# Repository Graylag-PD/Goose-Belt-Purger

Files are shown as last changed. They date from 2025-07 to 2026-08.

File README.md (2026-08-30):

**BRANTA Branch** - This is a second major iteration of the GBP. Everything is work-in progress and anything can change withou warning, but if you want to testsome newest ideas, you are welcome. For more stable product look into an ANSER Branch
________________________________________

# Goose Belt Purger (GBP)
A simple, lightweight, and low-cost belt purger for 3D printers.\
An alternative to blob-producing purging routines and devices, or traditional purging into towers.\
Officially supported printers are Voron Trident and 2.4, but it is small and light enough to be adapted for other printers.

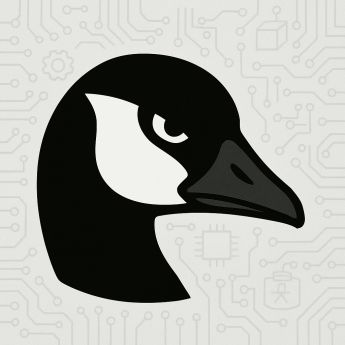
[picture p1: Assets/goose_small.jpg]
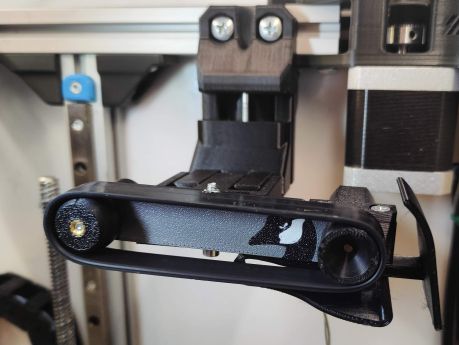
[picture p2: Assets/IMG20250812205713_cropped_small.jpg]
   
  
See also our [promo video](https://youtu.be/ZBZhAEFlKdA) on YouTube, or slightly older [video](https://youtu.be/MWTFuGqhi_c) with more detailed depiction of purger in action.
  
Currently in Beta testing — proven as a functional design, but can have unexpected issues and design might change any time.  
  
If you have any questions, you can visit my [Discord server](https://discord.gg/8a29q9gJb9).  
  
If you find this useful, a like or a make on [Printables](https://www.printables.com/model/1371713-goose-belt-purger-gbp) helps others discover and trust the design.

# About
Like many makers, I've been fascinated by single-nozzle multicolor/multimaterial printing. But like many, I hate purge towers. They can be large, ugly, and take up valuable print bed space. This is why I was intrigued by the Blobifier — but there are several issues. First, I use a Voron Trident, which isn't compatible. While there are adaptations of the Blobifier concept for the Trident, none have gained significant traction. Second, both the original Blobifier and its Trident adaptations generally share the drawback that each purge requires toolhead parking near the bed edge, blocking part of the bed and potentially risking collisions. Third, the produced blobs are volumetrically inefficient. Even though the blobs are relatively compact, their shape means they can't utilize the waste bin space effectively. This is even worse with the loose coil "poops" produced by some printers.

There had to be a better way.

And then it struck me — use a belt to produce compact "line" purges. To be fair, this isn't an entirely new idea. There have been mods involving purging on stationary aluminum platforms or kinematic belts, but none of those options felt right. I wanted something simple, affordable, and buildable from stuff you already have lying around your workshop.\
This is why the Goose Belt Purger was created.

What does it have to do with geese? Nothing. I just like geese.

# Design

The core of the GBP is a silicone wristband — the kind you can get anywhere, often for free. The most common size, which GBP is designed around, is 12 mm wide and 20 cm in circumference. You can use any similar band, even ones with embossing or printing, since we'll use the smooth inner surface. Changing the belt is easy, so use whatever you have and swap it later if needed.

Silicone rubber is ideal for this use. When filament is extruded onto the smooth side, it sticks but releases easily at the end of the straight belt section. Silicone is heat-resistant enough to endure the nozzle heat, provided it keeps moving. However, if the nozzle stays in one place too long, the band will discolor (brown or black) or even burn.

The belt moves along two printed pulleys. How does it stay in place without flanges? Dark magic. Don't ask.

One pulley is driven by a cheap miniature DC motor with a gearbox.  A 50rpm or slower version is recommended, up to 15rpm if you want really thick extrusions. &#x20;

> [!WARNING]\
> Motor is an inductive component. Skipping the recommended protection (e.g. flyback diode) can cause voltage spikes and permanent damage to your controller.  
>  
>Read the “Electrical connection” section and install all safety components.  
>Use at your own risk.  

The other pulley spins freely on a tilting arm. The arm pivots on a bearing around the motor shaft and is pushed upward by a pair of magnets acting as springs. The arm's purpose is to press against the nozzle but move away to avoid collisions with the nozzle or printhead.

GBP is mounted using an Armored Turtle brush mount or universal Klicky style mount. But you can also design your own mount and connect it with AT mount styled dovetails.

# Bill of Materials (BOM)
## Purger
- 1x Silicone wristband (12 mm wide, 200 mm circumference)
- 1x DC motor, 12 mm diameter, 6V/12V, 15rpm — commonly sold as GA12 N20 or N30. See note below.
- 3x 623 bearings
- 2x 6x3 mm magnets (Voron standard size)
- 3x heat-set insert M3x5x4 (Voron standard size)
  
If your board supports 5V on fan outputs, you may use a 6V motor. If only 24V is available, use a 12V motor with <50% PWM.  
Initial testing shows optimal belt speed under load is 2–12rpm, so the 15rpm seems to be ok. PWM can reduce speed to \~5–10% of rated speed. 30rpm and 50rpm motors also seem to be usable  

**M3 hardware:**

- 1x M3 nut
- 1x M3 nylock nut*
- 1x M3x6 set screw
- 1x M3x20 SHCS*
- 2x M3x20 FHCS
- 1x M3x30 SHCS
  
*) If you have trouble getting a M3 nyloc, you can instead use HSI variant of arm - replace nylock nut for one more heat-set insert, M3x16 SHCS instead of M3x20 SHCS and get some threadlocker  

**Electrical components:**
- Schottky diode 1A (e.g. 1N5819) - For 5V or 12V supply voltage  
or
- Schottky diode 2A (e.g. 1N5820) - For 24V supply voltage together with 12V motor  
- Resistor 47R
- Ceramic capacitor 10 nF, 50V 
  
If you don't like the idea of soldering those parts, you can also get yourself a **[MicroFlip](https://github.com/Trondle-Embeeded-Systems/MicroFlip)** board, which already has everything.

## Mounts
**AT mount**  
Applies to Voron Trident or similar printer together with modified (shorter) AT mount files  
- 2x heat-set insert M3x5x4 (Voron standard size)
- 2x M3 nyloc nut
- 2x M3x8 SHCS
- 1x M3x35 SHCS (you can use M3x30 if you have trouble getting it)
- 1x M3x25 SHCS

**Klicky style mount**  
Universal solution  
- 8x heat-set insert M3x5x4 (Voron standard size)
- 8x M3x8 SHCS

# Build Instructions

Build instructions can be found [here](assembly.md).

# Electrical Connection

Connect the DC motor to any free power output on your controller board, preferably a fan output. If possible, supply it with 5V or 12V to minimize heating. Otherwise, reduce voltage via PWM.

> [!IMPORTANT]\
> The DC motor is a strong inductive load and will generate large voltage spikes, which can destroy your board's MOSFET or even the MCU if untreated. At minimum, use a properly sized Schottky flyback diode across the board output. I also recommend an RC snubber on the motor terminals.
>
> Some boards (e.g., BTT Octopus) already include protection diodes. Others rely only on the MOSFET's internal diode, which is usually insufficient. You can check comprehensive table [here](board_list.md), or consult your board's schematic.  When unsure, ask someone.
>
> For the RC snubber, I used a 47 Ω resistor and a 10 nF, 50V ceramic capacitor. Solder one leg of each component together, then solder the free legs to the motor terminals. This configuration dampens voltage spikes while preserving PWM response. You may use a larger capacitor for extra safety, but note that increased capacitance degrades PWM response. Avoid using a capacitor alone (without resistor), as this can cause resonance and make things worse.

I confirmed the effectiveness of these measures with an oscilloscope, but I can't guarantee that no fast transients were missed (e.g., during PWM changes). Data is still limited, so proceed with care and understand what you're doing.

If you want some better alternative to manually soldering components to motor, see amazing [MicroFlip](https://github.com/Trondle-Embeeded-Systems/MicroFlip) project by Ntrondle. You can make it yourself, or check our Discord if anyone has any boards for sale. Keep in mind, that MicroFlip is **not** developed as part of this project. If you like it and would like to support its creator, do so on his GitHub page.  

# Software and Slicer Configuration
For more information about provided configuration file, slicer configuration and integration into AFC or Happy Hare, please look [here](sw_configuration.md).

# Tips and Observations
 
Extrude onto the smooth inner side of the wristband. You can try the outer side, but adhesion is generally worse and requires an unembossed, unprinted band — which is surprisingly hard to find. The inner surface sticks well, even without direct nozzle contact, while the outer side requires pressure that magnets alone can't provide.

Adhesion heavily depends on belt speed. If filament doesn't stick, slow the belt. Once adhesion starts, the extruded line tends to pull more material from the nozzle. 
  
Adhesion is also strongly dependant on filament drynes. Wet filament tends to curl up and does not stick to belt as easilly.

The macro splits the purge into short "toothpicks" or pellets to improve waste volume efficiency.

Initial testing shows optimal belt speed is 2–12rpm (roughly 1.8–11 mm/s or 108–660 mm/min). The easiest way to measure speed is to mark a spot on a pulley, start a stopwatch, and time 10 full revolutions.

Don't be afraid to experiment with the macro parameters. Every printer is unique, so expect to tune it up for a some time untill you hit the 'just right' zone.

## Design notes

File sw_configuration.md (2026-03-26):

# Configuration file and macro configuration
Default control software is the [Goose Purge Macro](https://github.com/Graylag-PD/Goose-Purge-Macro). For details on installation, see there.  
Information in this file apply to macro version v0.8.2 or newer. If you have any kind of issues, check first, if you are on newest available version.  
  
The old version of the macro (v0.7.3) remains within the Goose Belt Purger repository and is now considered a legacy solution. 

## Macro configuration
Macro can be configured by changing the variables in `goose_purge.cfg` file. See comments in the file and adapt it to your printer.  

Once set up, the purge routine can be triggered by running the G-code macro:  
 - `GOOSE_PURGE PURGE_VOLUME=###`  
   or  
 - `GOOSE_PURGE PURGE_LENGTH=###`  
where ### is the purge volume in mm³ or length in mm. If both are provided, they are added up. If neither is provided, the macro runs according default value variable configured within the macro.

Below are the most common "chokepoints" for the new users:  
### Output pin definition
This part is usually straight forward and the only difficulty may come from identifying correct MCU pin(s). For this you need to consult your board documenatation.  
  
For a DC motor, use a fan output. There is hovewer a catch - although any fan output can be used, or in fact any output pin, not all pins are capable of a HW PWM and this may apply even to pins which should be HW PWM capable from chip design. 
This is not a bug, but comes from the way Klipper is configured. If you run into situation, that everything is connected and configured correctly but the motor still does not activates, consider changing the output which you are using.  
If for whatever reason you cannot use any other port, you may fall back to using the SW generated PWM, but be aware of the performance penalty this can mean.   
One example of the pin which should work but does not is the PA8 on a STM32F446.
  
### Z axis strategy
Applicable Z axis strategy depends on the purger mounting and printer type. For a Voron Trident (or similar) printers you should use "0" - no Z movement. For a Voron 2.4 and purger on the gantry you can use either strategy "0" or strategy "2". Later can help with pellets pilling up under the purger.  
For a Voron 2.4 with the purger fixed on a frame, use strategy "1" - absolute Z position.
  
### Staging and purging positions
At first you should think about your purging position. In general you have two options - either purge directly on top of your idler pulley, or to purge on a free belt span (in between pulleys). If you are in doubt, start with purging position above the idler belt, as the pressure from the idler creates more stable conditions and it maximises the cooling time for the deposited material.  
Purging on a free belt span is often used by more experienced users who aim to maximise purge thickness (to create short, thick pellets), as the belt flexes and adapts better to thick extrusions.  
  
Once you decide on your purging position, you can define your staging position. In general your staging can be anywhere, as its only purpose is to have defined safe position from which we can reach the purging position. But in practice you need to consider oozing and as such you should have your staging position as close to purging position as possible AND have it so, that by moving to purging position you wipe away any ooze. This usually means perpendiculary to the belt or between motor pulley and purging position. If you do this wrong, the ooze might be squished to the side of the nozzle where it sticks and later on causes issues.    

### Motor PWM (belt_pwm variable)
Although this parameter should be easy to configure, unfortunately there is a great variability between motors which you can buy. Some n20 motors are built for a high torque and spin well even with very low PWM duty cycles, while some motors are built for a lower torque and need considerable higher PWM. This can be most easily identified by the static coil resistance, but unfortunately this parameter is usually listed in the item description.  
Fortunately there is a simple way to determine the necessary values. Connect your (fully assembled) purger to the printer, configure the macro with a default values and restart the klipper. As soon the printer comes back online, you should see the purger in your interface (Mainsail or FLuidd) along the fans with option to control its speed with a slider. This way you can quickly try out various PWM settings without actually running the macro.  
When testing the motor, you are looking at three different thresholds. First one is the minimum start-up speed - this is the PWM value at which the motor reliably starts even from standstill. This is your safe value which you should ideally put to your macro. Next up is the minimum stable speed - this is the PWM value, at which the motor can still run reliably if kickstarted. This is usually 10% below minimum start-up speed and you can use it with correctly set kickstart paramerer. Keep in mind, that the purging itself is loading the motor and can stall it if you go too low.  
Third value is the absolute lowest speed - this is the speed, at which the motor is still able to run, but tends to stall at any kind of load. This is usually 5% below minimum stable speed. There is no practical use for this setup.  
  
Once you find the value you are happy with, set it to the macro variables, restart the klipper and do the test run of the macro just to see, that everything works as expected. 

## Useful tips
Tuning the variables "just right" can take many iterations and hitting that Save&Restart button every time can be very time consuming. Instead, you can edit your variables on the fly through terminal command `SET_GCODE_VARIABLE`, e.g. `SET_GCODE_VARIABLE MACRO=_GOOSE_PURGE_VARIABLES VARIABLE=belt_pwm VALUE=0.33` to change the belt speed. You can even do that during print job - set up a test print that has a bunch of filament changes, then adjusted the variables live as you go. Because the way klipper queues up gocode, it may not take effect immediately so if you enter this while you're in the middle of a toolchange, you won't see the results until the next toolchange.  
Keep in mind this doesn't save the values to config file, so you will have to remember to set the values in the cfg file yourself. 

## GBP and other printer firmwares
No other printer firmwares are supported as of this moment. We are open to add support for other firmwares if you are interested, however be prepared to provide extensive support for a development for your choosen platform.

# Integration of Goose Belt Purger into your print jobs

## Standalone operation (Slicer controlled)
You can use GBP in standalone mode independently on any other klipper add-ons. You can even use it this way if you don't have any MMU/AMS on your printer, e.g. for manual filament changes. Purging can be triggered manualy, or more commonly by slicer.  

Slicer configuration is following:  
For initial priming, place the `GOOSE_PURGE` command with appropriate parameter at the beginning of your **Start G-code** where you'd normally place a prime line.  
For tool changes, insert the command into **Tool change G-code** just after the `T#` command.  
Note that not all slicers support passing purge parameters. In OrcaSlicer, you can use `GOOSE_PURGE PURGE_LENGTH=[flush_length]`. In PrusaSlicer, the volume must be hardcoded.  For other slicers, consult their documentation. 

If you are using GBP in standalone mode but let filament changes handling to Happy Hare or a similar tool, configure it so it doesn't return toolhead to the previous or next G-code position to avoid unnecessary travel.  

## AFC integration 
*Contributed in full by adamcstorm*  
To integrate with AFC-Klipper-Add-On:  

Modify `AFC.cfg`. Under the Macro Config section, change the poop settings to use the goose_purge macro, and disable the kick option:  
```
# Poop Settings
poop: True                      # Enable Poop.
poop_cmd: GOOSE_PURGE           # Poop macro name.

# Kick Settings
kick: False                     # Enable Kick.
kick_cmd: AFC_KICK              # Kick macro name.
```
All other settings can be enabled/disabled per your preference.  
Of note, if you have wipe enabled, the wipe routine will be called twice. This is due to the default AFC order of operation that wipes both before and after the kick routine. Since we have disabled the kick routine, it performs the wipe twice in a row. It is recommended to disable the wipe option in `AFC.cfg`, and instead call the brush routine within the `goose_purge` macro by modifying the user_end_script variable: `variable_user_end_script: 'AFC_BRUSH'`.

GBP is compatible with the default AFC method of passing the variable purge length from the slicer to the print via gcode. To configue this, follow this guide:  
https://www.armoredturtle.xyz/docs/afc-klipper-add-on/features.html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.  
Be aware, that the GBP macro does not access the AFC variables and as such ignores the AFC's variable `variable_purge_lenght`. Instead you should configure GBP's own variable `variable_default_purge_volume`. This value gets used only when no purge parameters are provided, such as during initial load. 

## Happy Hare integration
Happy Hare takes rather complex approach to purging. Unlike other methods it does not rely on slicer to pass purge volume or length together with toolchange. Instead it works with internal purge volume matrix and further enhances it by adding volume of residual filament and cut tip fragment. It can get its purge volume matrix either from internal toolmap or from processing gcode metadata. Either way, for purging to work you need to make sure, that your instance of Happy Hare processes this data correctly. For more information, please visit Happy Hare documentation here:  
https://github.com/moggieuk/Happy-Hare/wiki/Tip-Forming-and-Purging

Also please note, that even if your Happy Hare is configured correctly, it relies on slicer to pass the purging matrix correctly.  

As for actual integration, this is very straightforward and the only thing you need to do is edit `mmu_parameters.cfg` by setting handle `purge_macro: '_goose_purge_hh'` without any parameters.  
The only thing to keep in mind is that the `purge_macro:` handle is case sensitive, so you need to watch your capitalization.
  
Note, that we are not calling directly `GOOSE_PURGE` macro, but instead its wrapper `_goose_purge_hh`. This is due to how Klipper resolves macros and passes parameters.
  
Happy Hare does not have any wiping logic embedded, so if you want automatic wiping execution after purge, consider adding your custom wiping macro to the `variable_user_end_script:''` in `goose_purge.cfg`.

## Other filament management add-ons
No other filament management add-ons are supported as of this moment. You are free to develop integration into other add-ons and if you do, we can list them here, however be prepared to support such solution. 

# Advanced Slicer configuration
Following paragraphs are not mandatory for the purger operation, however may improve your experience and print results.  

## Purger operation together with a prime tower (Orca Slicer)
Although the Goose Belt Purger can completely eliminate purge and prime towers, going to the print object directly after purging, some users report issues with oozing debris contaminating the print and prefer to use a small prime tower along the purger. This means they do the purging on the GBP, but then follow up with the prime tower, where they catch any possible debris and stabilize the nozzle pressure.  
The Orca Slicer has a provision for this kind of a setup - to enable this, you need to enable the prime tower in the global setting, but disable the **Purge in prime tower** in the Printer settings.

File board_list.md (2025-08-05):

# List of boards with or without flyback diodes
This is list of 32bit boards from common vendors with open source documentation and details whether specific board does or does not have protective flyback diodes on its outputs.  
List is created manualy and verified by me personaly based on schematics. If you have any board not listed or do you have any new or conflicting information, let me know.  
  
In some cases it is noted, that 1A Schottky or 1A rectifier diode is used. 1A Schottky is perfectly fine if you have snubber soldered and you use 6V motor at 5V or 12V motor at 12V, but can be a risk for 12V motor at 24V. 
Although this should still work, diode could be damaged over long time, especially if its not properly cooled. Use it at your own risk, or simply add another Schottky directly to motor clamps.  
1A rectifier diode is different story though. Plain rectifier diode is not fast enough to operate at 25 kHz PWM and will be mostly inefficient. You could try to lower your PWM frequency below 1kHz, but it is highly recommended to disregard this diode and add Schottky directly to motor.
  
## BTT
<table>
  <tr>
    <th>Board identification</th>
    <th>Diode on fan outputs?</th>
    <th>Diode on power outputs?</th>
    <th>Note</th>
  </tr>
  <tr>
    <td>Octopus /Pro/Max</td>
    <td>Yes</td>
    <td>Yes</td>
    <td>All versions</td>
  </tr>
  <tr>
    <td>Manta M8P V1/V2</td>
    <td>Yes</td>
    <td>Yes</td>
    <td></td>
  </tr>
  <tr>
    <td>Manta M5P V1</td>
    <td>Yes</td>
    <td>Yes</td>
    <td></td>
  </tr>
    <tr>
    <td>Manta M4P V2</td>
    <td>Yes</td>
    <td>Yes</td>
    <td>1A Schottky</td>
  </tr>
  <tr>
    <td>Manta E3EZ V1</td>
    <td>Yes</td>
    <td>No</td>
    <td>1A Schottky</td>
  </tr>
  <tr>
    <td>SKR Pico V1</td>
    <td>Yes</td>
    <td>No</td>
    <td>1A Schottky</td>
  </tr>
  <tr>
    <td>SKRat V1</td>
    <td>Yes</td>
    <td>Yes</td>
    <td></td>
  </tr>
  <tr>
    <td>Kraken V1</td>
    <td>Yes</td>
    <td>Yes</td>
    <td></td>
  </tr>
  <tr>
    <td>SKR 3 /EZ</td>
    <td>Yes</td>
    <td>Yes</td>
    <td></td>
  </tr>
  <tr>
    <td>SKR V1.1/1.3/1.4/2</td>
    <td>No</td>
    <td>No</td>
    <td></td>
  </tr>
  <tr>
    <td>SKR mini V1.1</td>
    <td>No</td>
    <td>No</td>
    <td></td>
  </tr>
  <tr>
    <td>SKR Pro V1.1/1.2</td>
    <td>No</td>
    <td>No</td>
    <td></td>
  </tr>
  <tr>
    <td>SKR MINI E3 V3</td>
    <td>see note</td>
    <td>see note</td>
    <td>1A rectifier diode</td>
  </tr>
  <tr>
    <td>SKR MINI E3 V1/V1.2/V2</td>
    <td>No</td>
    <td>No</td>
    <td></td>
  </tr>
  <tr>
    <td>E3 RRF</td>
    <td>No</td>
    <td>No</td>
    <td></td>
  </tr>
  <tr>
    <td>SKR E3 DIP/Turbo</td>
    <td>No</td>
    <td>No</td>
    <td></td>
  </tr>
  <tr>
    <td>GTR</td>
    <td>No</td>
    <td>No</td>
    <td></td>
  </tr>
</table>

## Fysetc
<table>
  <tr>
    <th>Board identification</th>
    <th>Diode on fan outputs?</th>
    <th>Diode on power outputs?</th>
    <th>Note</th>
  </tr>
  <tr>
    <td>Spider King</td>
    <td>Yes</td>
    <td>Yes</td>
    <td>Diode type not specified, presumed to by 1A Schottky</td>
  </tr>
  <tr>
    <td>Spider Pro</td>
    <td>Yes</td>
    <td>No</td>
    <td>1A Schottky</td>
  </tr>
  <tr>
    <td>Spider V2.3/V3/V3 H7</td>
    <td>Yes</td>
    <td>No</td>
    <td>1A Schottky</td>
  </tr>
  <tr>
    <td>Spider V1/V2.2</td>
    <td>No</td>
    <td>No</td>
    <td></td>
  </tr>
  <tr>
    <td>Cheetah V1/2/3</td>
    <td>No</td>
    <td>No</td>
    <td></td>
  </tr>
  <tr>
    <td>Cheetah Mix</td>
    <td>No</td>
    <td>No</td>
    <td></td>
  </tr>
  <tr>
    <td>Catalyst Main Board</td>
    <td>No</td>
    <td>No</td>
    <td></td>
  </tr>
  <tr>
    <td>S6</td>
    <td>No</td>
    <td>No</td>
    <td></td>
  </tr>
  <tr>
    <td>R4</td>
    <td>Yes</td>
    <td>Yes</td>
    <td>1A Schottky</td>
  </tr> 
  <tr>
    <td>R4</td>
    <td>Yes</td>
    <td>Yes</td>
    <td>1A Schottky</td>
  </tr> 
</table>

## Mellow
Mellow documentation can be difficult to understand. For some boards they drawed some diodes, but without any additional details. It is recommended to treat those boards as NOT protected unless confirmed otherwise.
<table>
  <tr>
    <th>Board identification</th>
    <th>Diode on fan outputs?</th>
    <th>Diode on power outputs?</th>
    <th>Note</th>
  </tr>
  <tr>
    <td>Fly Super8 /Pro</td>
    <td>Yes?</td>
    <td>Yes?</td>
    <td>Unclear documentation</td>
  </tr>
  <tr>
    <td>Fly Super5Pro</td>
    <td>Yes?</td>
    <td>Yes?</td>
    <td>Unclear documentation</td>
  </tr>
  <tr>
    <td>Fly Gemini V1/1.1/2/3</td>
    <td>Yes?</td>
    <td>Yes?</td>
    <td>Unclear documentation</td>
  </tr>
  <tr>
    <td>Fly E3 V2</td>
    <td>Yes?</td>
    <td>Yes?</td>
    <td>Unclear documentation</td>
  </tr>
  <tr>
    <td>Fly RRF E3</td>
    <td>No</td>
    <td>No</td>
    <td></td>
  </tr>
  <tr>
    <td>Fly E3 Pro V1/2/3</td>
    <td>No?</td>
    <td>No?</td>
    <td>Unclear documentation</td>
  </tr>
  <tr>
    <td>Fly Puppet</td>
    <td>Yes</td>
    <td>No</td>
    <td></td>
  </tr>
  <tr>
    <td>Fly CDY V3</td>
    <td>Yes?</td>
    <td>Yes?</td>
    <td>Diode type not specified, could be rectifier diode</td>
  </tr>
  <tr>
    <td>Fly CDY V1/2</td>
    <td>No</td>
    <td>No</td>
    <td></td>
  </tr>
  <tr>
    <td>Fly Mini</td>
    <td>No</td>
    <td>No</td>
    <td></td>
  </tr>
</table>

## MKS
<table>
  <tr>
    <th>Board identification</th>
    <th>Diode on fan outputs?</th>
    <th>Diode on power outputs?</th>
    <th>Note</th>
  </tr>
  <tr>
    <td>Monster8 V1/V2</td>
    <td>see note</td>
    <td>see note</td>
    <td>1A rectifier diode</td>
  </tr>
  <tr>
    <td>OWL V1</td>
    <td>see note</td>
    <td>see note</td>
    <td>Diode type not documented, presumed to be 1A rectifier diode</td>
  </tr>
  <tr>
    <td>SKIPR V1</td>
    <td>see note</td>
    <td>see note</td>
    <td>Diode type not documented, presumed to be 1A rectifier diode</td>
  </tr>
  <tr>
    <td>Robin (All versions)</td>
    <td>No</td>
    <td>No</td>
    <td>Includes Robin, Robin2, Pro, Mini, Nano1/2/3, Lite1/2/3, E3/E3D</td>
  </tr>
  <tr>
    <td>Eagle</td>
    <td>No</td>
    <td>No</td>
    <td></td>
  </tr>
  <tr>
    <td>TinyBee</td>
    <td>No</td>
    <td>No</td>
    <td></td>
  </tr>
    <tr>
    <td>SBASE/SGEN</td>
    <td>No</td>
    <td>No</td>
    <td>Includes SGEN_L V1/2 </td>
  </tr>

</table>

## LDO
<table>
  <tr>
    <th>Board identification</th>
    <th>Diode on fan outputs?</th>
    <th>Diode on power outputs?</th>
    <th>Note</th>
  </tr>
  <tr>
    <td>Leviathan V1.3</td>
    <td>Yes</td>
    <td>No</td>
    <td>1A Schottky</td>
  </tr>
  <tr>
    <td>Leviathan V1.2</td>
    <td>No</td>
    <td>No</td>
    <td></td>
  </tr>
</table>

</table>

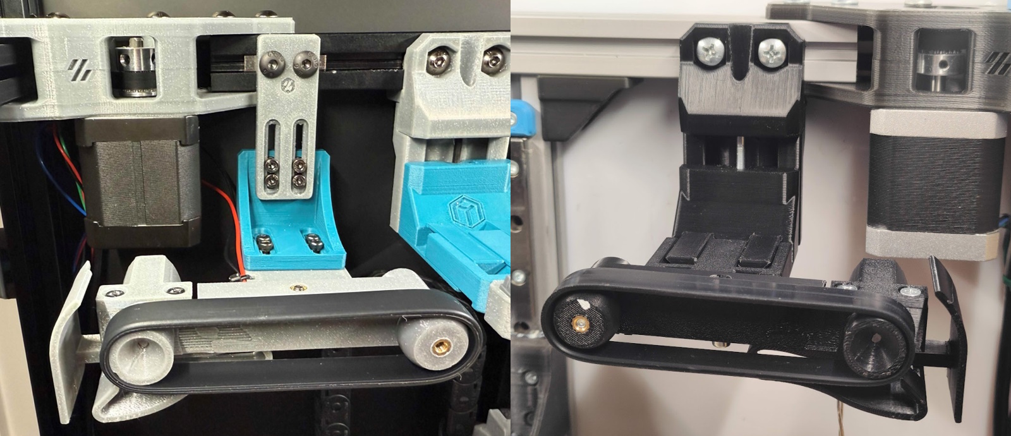
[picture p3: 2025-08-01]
Assets/Purgers.jpg

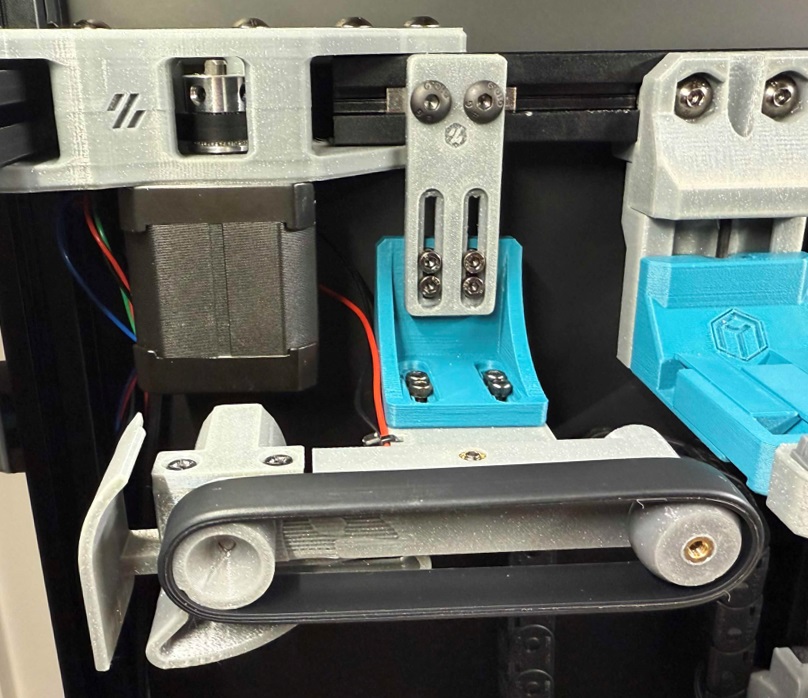
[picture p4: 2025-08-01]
Assets/IMG_1006_cropped.jpg

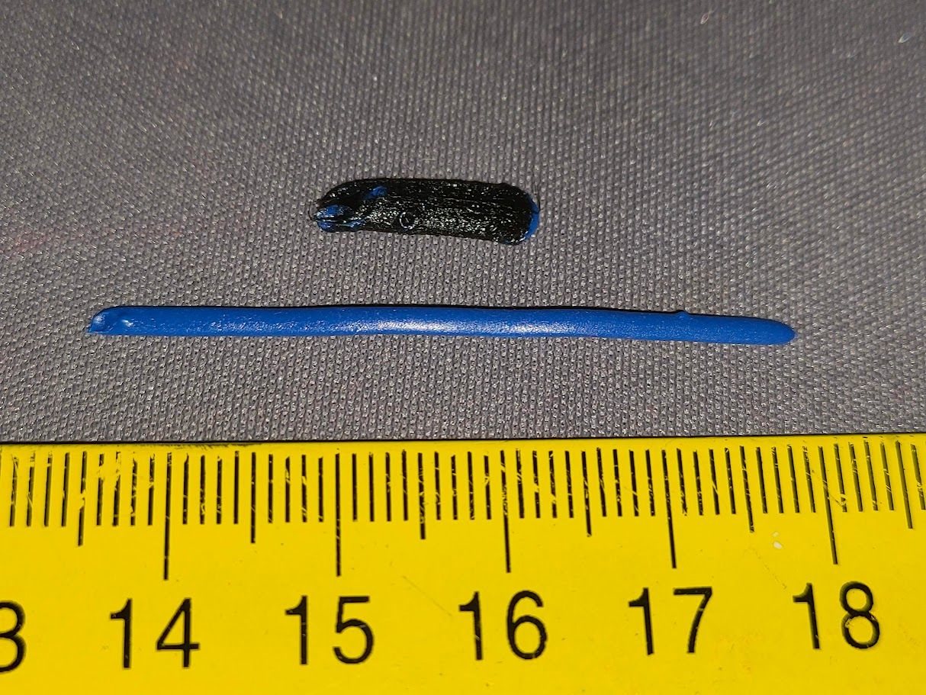
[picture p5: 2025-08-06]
Assets/gbp_waste.jpg

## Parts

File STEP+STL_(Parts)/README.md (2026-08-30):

# Instructions for printing
Use standard Voron print settings (see below). Recommended material is ABS/ASA. Parts are oriented for print. No supports are required, deflector has integrated support.  

Layer height: 0,2 mm  
Extrusion width: 0,4 mm  
Infill: 40%  
Wall count: 4  
Solid top/bottom layers: 5  

# Which parts to print
Choose files from either STEP or STL folder. STEP files are recommended.   

## Base version parts
**GBP_Frame**  
**GBP_Arm**  
**GBP_Motor_cover**  
**GBP_Motor_pulley**  
**GBP_Idler**  
**GBP_Bearing_spacer**  
**GBP_Deflector**  

## Alternative Parts
**GBP_Arm_nyloc** - Arm variant with a nyloc nut  
**GBP-Arm_HSI** - Same as default Arm 
**GBP_Deflector_long** - Same as default Deflector  
**GBP-Deflector_short** - Shorter version of deflector, designed to prevent collision with nozzle. To be used when purger is mounted closer to the printer center  
**GBP-Deflector_lite** - Part version with only scraper (no deflecting cover) for cleaner look  
**GBP-Deflector_long_noinserts** - Same as long, but with screws in plastic instead of inserts  
**GBP-Deflector_short_noinserts** - Same as short, but with screws in plastic instead of inserts  
**GBP-Deflector_lite_noinserts** - Same as lite, but with screws in plastic instead of inserts
**GBP-Idler(+ 0)** - Basic version of idler. Designed under assumption, that arm is perfectly perpendicular to motor axis and that it does not flex. If your wristband tends to walk towards motor, use this one. 
**GBP_Idler(+ 1,5)** - Same as default Idler  
**GBP-Idler(+ 3,0)** - Extra offseted version of idler. If your wristband tends to walk towards bed, try this one.  

## Multicolor Parts
Choose appropriate version  
**GBP_Arm_multicolor_nyloc**  
**GBP_Arm_multicolor_HSI**  
STEP files are saved as multibody assembly and can be loaded directly. STL files are saved as multiple files, which need to be loaded together  

## Mounts
Select the appropriate files from Mounts folder, depending on your printer

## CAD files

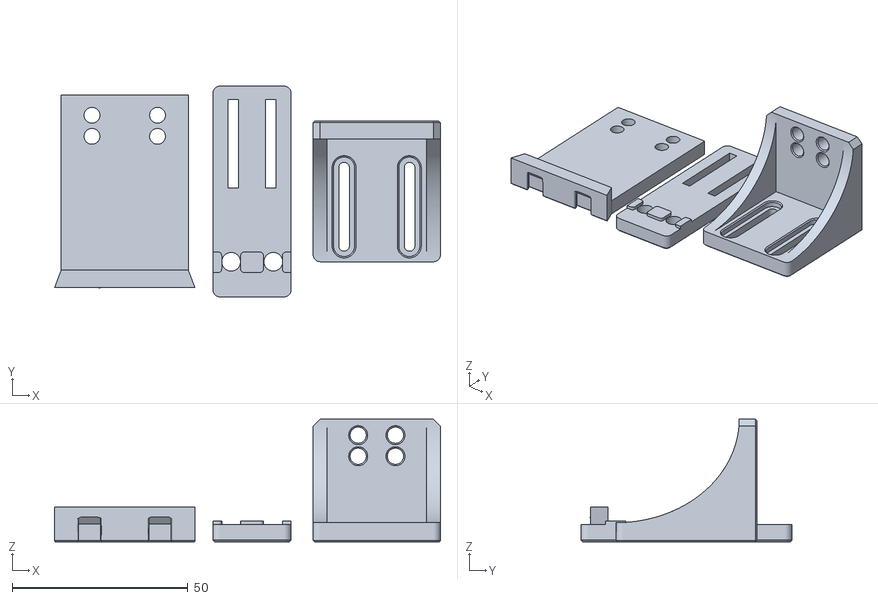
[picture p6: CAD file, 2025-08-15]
STEP+STL_(Parts)/STL/05_Plates/Klickystyle_complete_long.stl
109.9 x 60.0 x 35.0

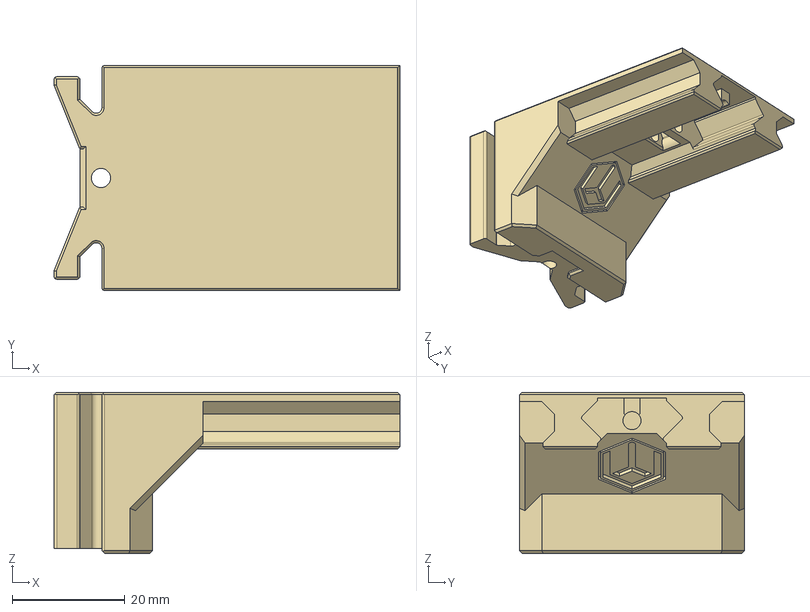
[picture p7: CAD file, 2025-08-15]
STEP+STL_(Parts)/STEP/01_Mounts/ArmoredTurtle_Brush_mount/[a]_front_arm_base.step
61.5 x 40.0 x 28.6 mm

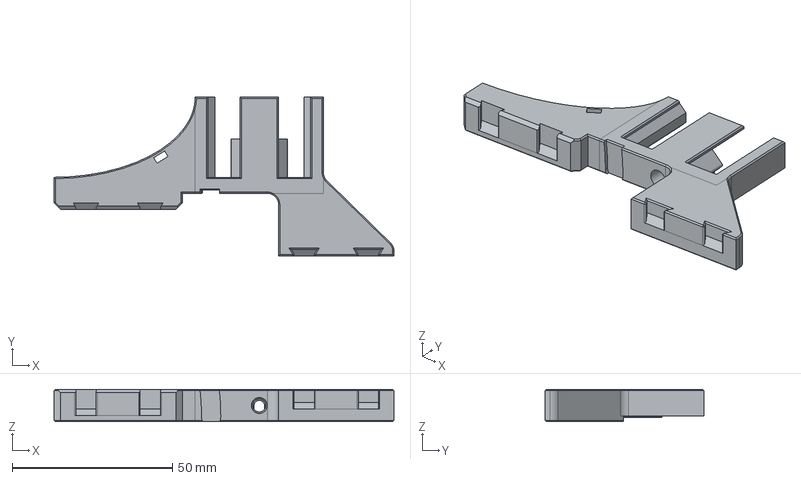
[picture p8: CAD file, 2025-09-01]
STEP+STL_(Parts)/STEP/01_Mounts/AT_Style-Voron_Trident+2.4/ATmount_front_arm_slide_offseted_am04.step
106.0 x 49.5 x 10.0 mm

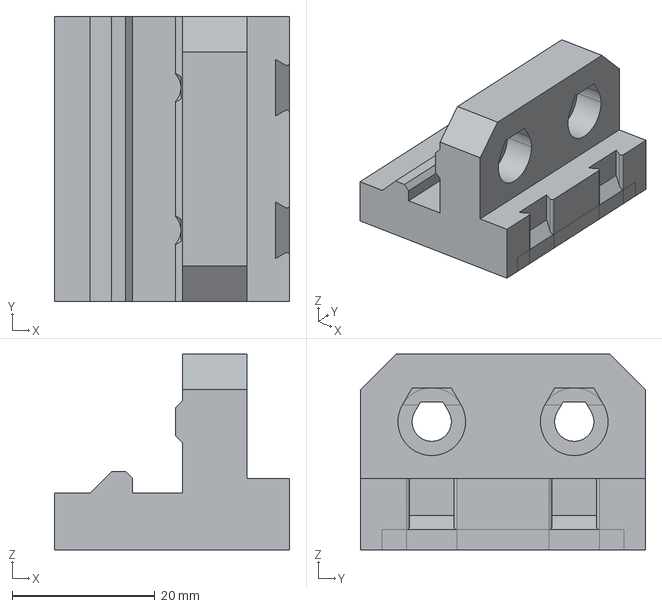
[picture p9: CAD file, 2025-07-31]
STEP+STL_(Parts)/STEP/01_Mounts/Mercury_One/Mercury1_GBP_mount_front.step
33.0 x 40.0 x 27.5 mm

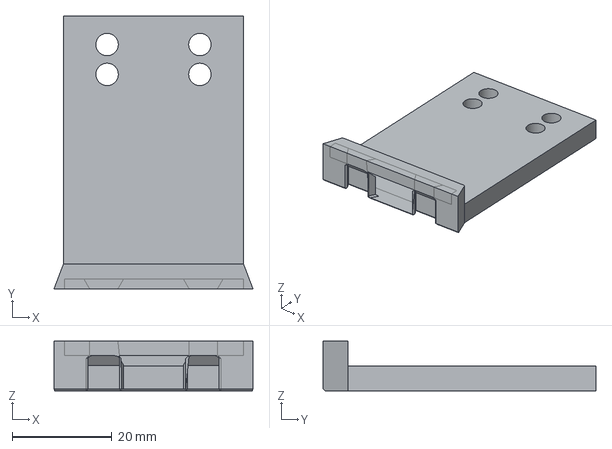
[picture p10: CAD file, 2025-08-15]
STEP+STL_(Parts)/STEP/01_Mounts/Universal_Klicky_style/Klickystyle_horizontal.step
40.0 x 54.8 x 10.0 mm

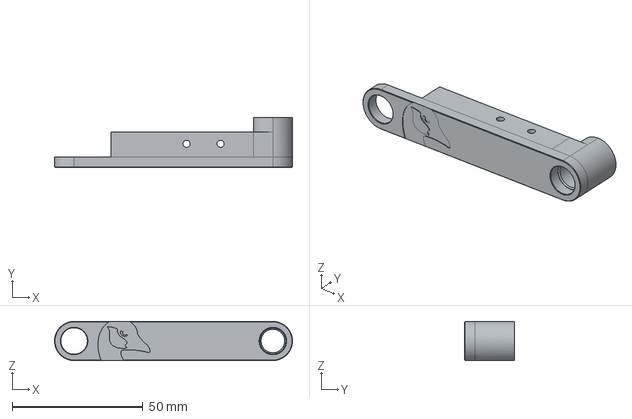
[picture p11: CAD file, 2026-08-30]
STEP+STL_(Parts)/STEP/02_Alternative_parts/GBP_Arm_HSI.step
91.0 x 19.0 x 15.0 mm

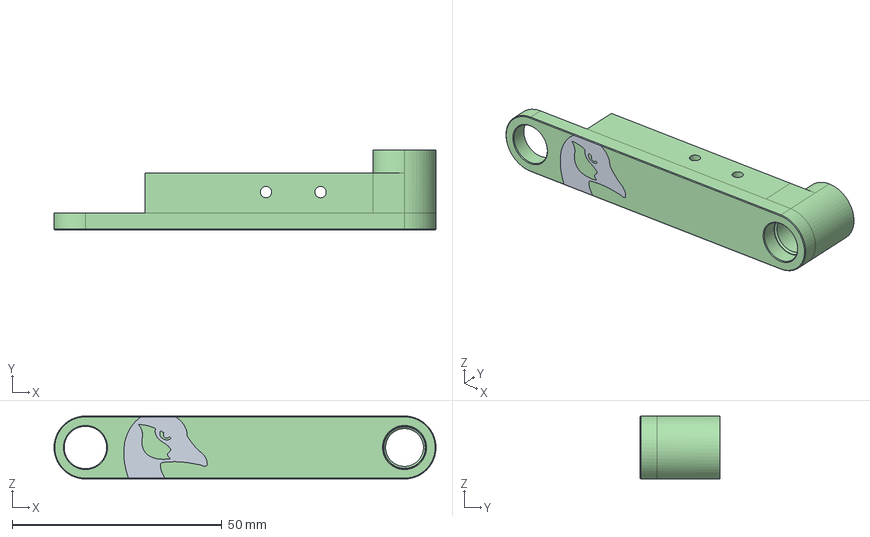
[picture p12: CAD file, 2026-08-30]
STEP+STL_(Parts)/STEP/03_Multicolor_arm/GBP_Arm_multicolor_HSI.step
91.0 x 19.0 x 15.0 mm
Arm_goose_outline
Arm_goose_cheek
Arm_goose_eye
Arm__base_HSI

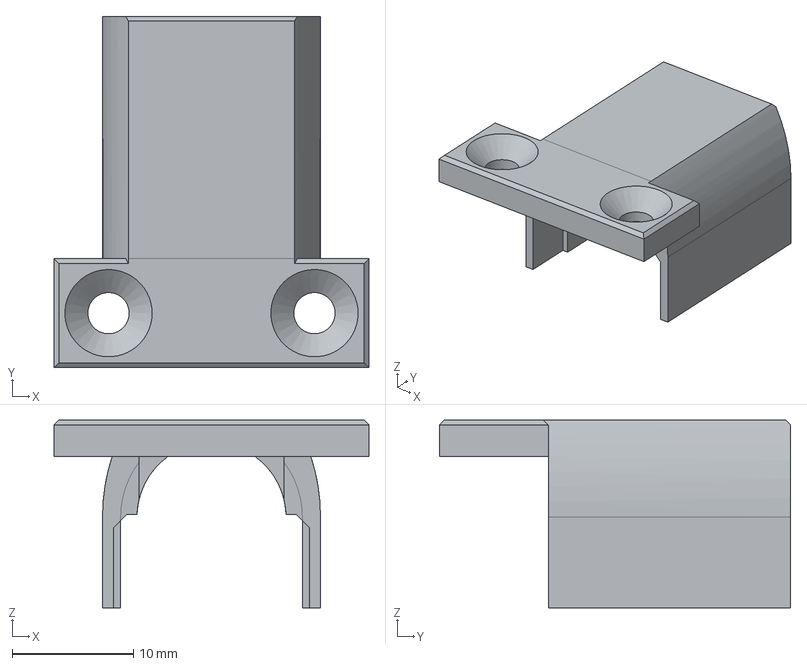
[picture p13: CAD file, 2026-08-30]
STEP+STL_(Parts)/STEP/GBP_Motor_cover.step
26.0 x 29.0 x 15.5 mm

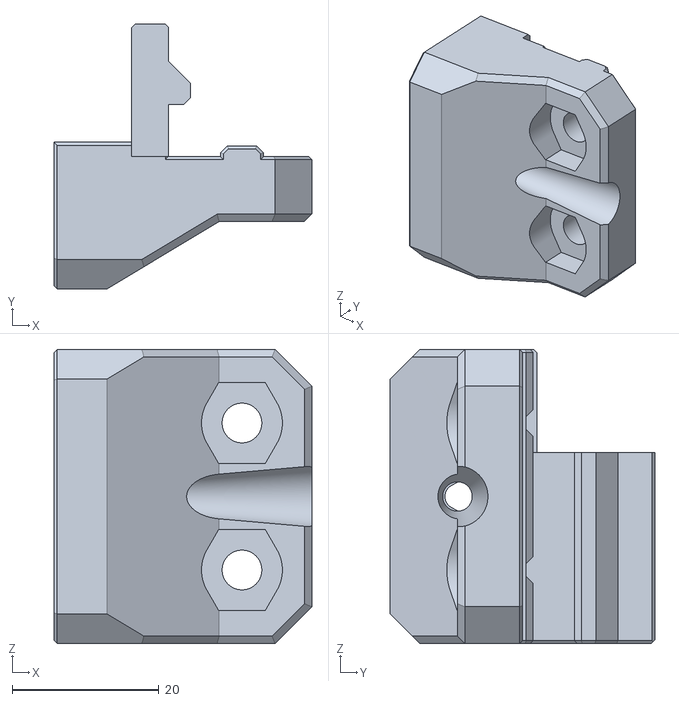
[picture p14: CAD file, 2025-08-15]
STEP+STL_(Parts)/STL/01_Mounts/AT_Style-Voron_Trident/ATmount_upper_(GBP).stl
35.0 x 36.0 x 40.0

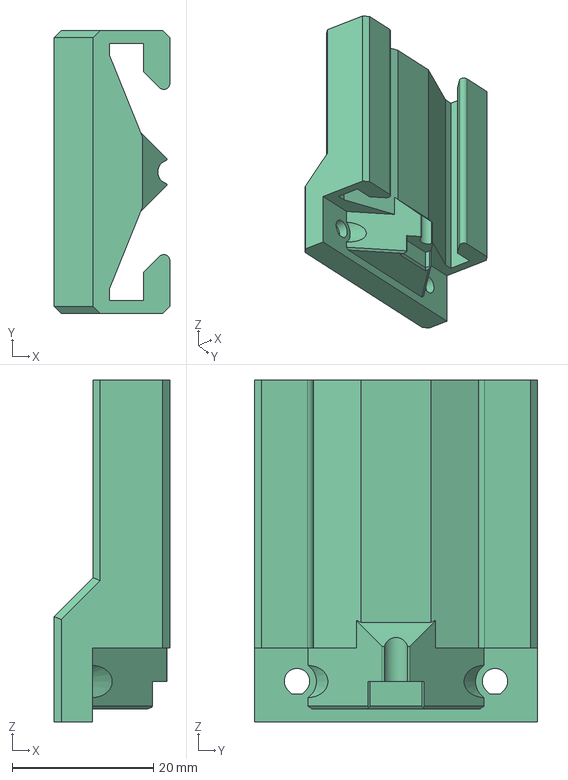
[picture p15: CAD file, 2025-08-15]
STEP+STL_(Parts)/STEP/01_Mounts/ArmoredTurtle_Brush_mount/mount_lower.step
16.4 x 40.0 x 48.4 mm

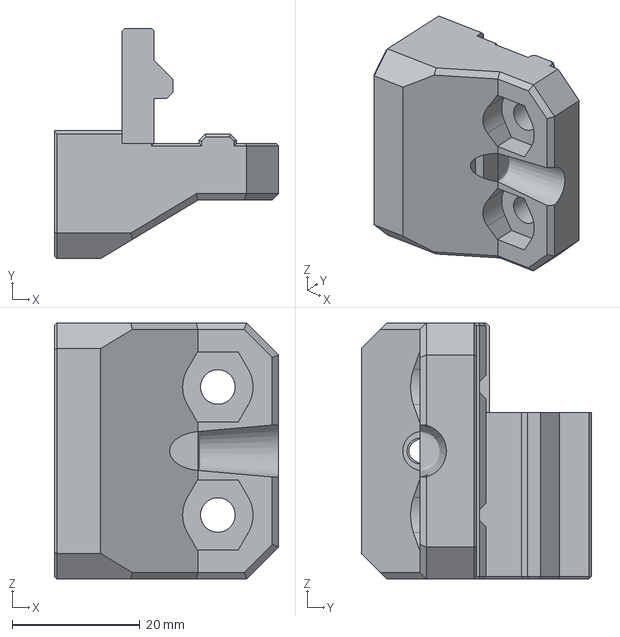
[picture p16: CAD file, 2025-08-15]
STEP+STL_(Parts)/STEP/01_Mounts/AT_Style-Voron_Trident+2.4/ATmount_upper_(GBP).step
35.0 x 36.0 x 40.0 mm

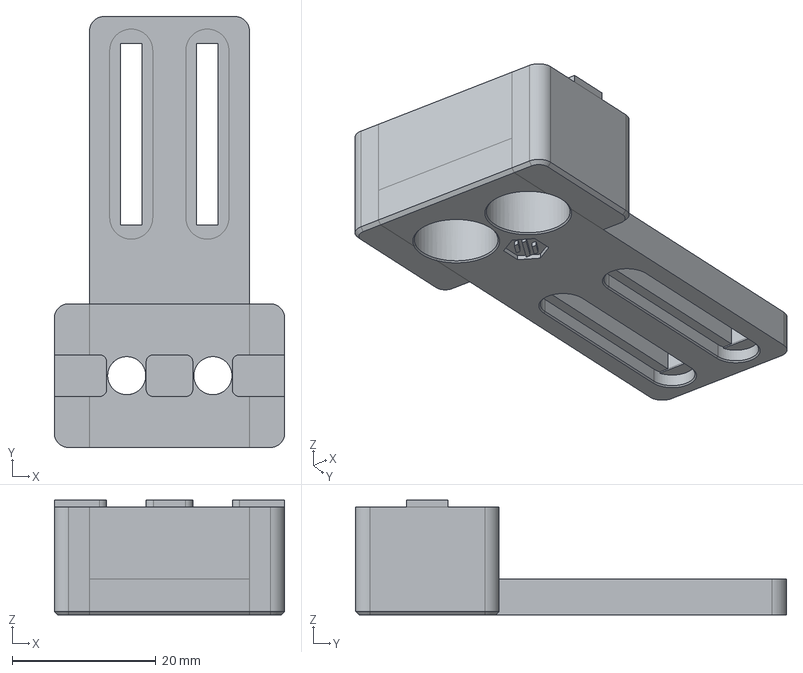
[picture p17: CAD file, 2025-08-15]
STEP+STL_(Parts)/STEP/01_Mounts/Universal_Klicky_style/Klickystyle-offseted-long.step
32.1 x 60.0 x 16.0 mm

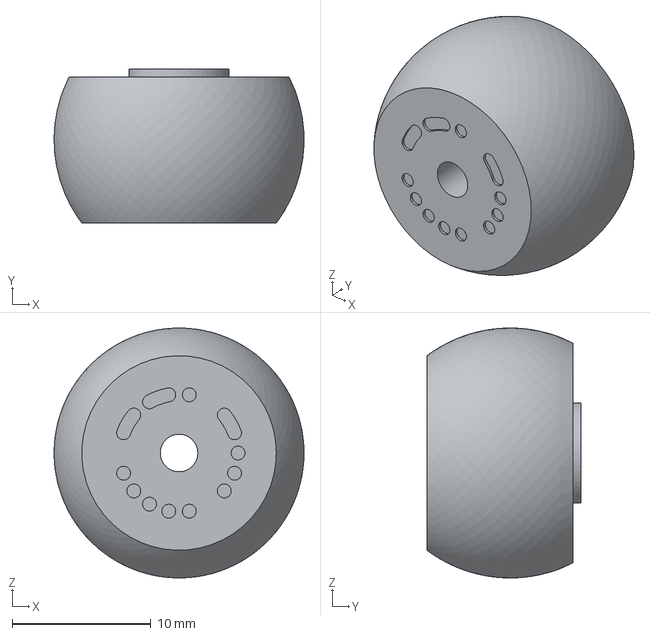
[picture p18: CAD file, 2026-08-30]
STEP+STL_(Parts)/STEP/02_Alternative_parts/GBP_Idler(+1,5).step
18.0 x 11.1 x 18.0 mm

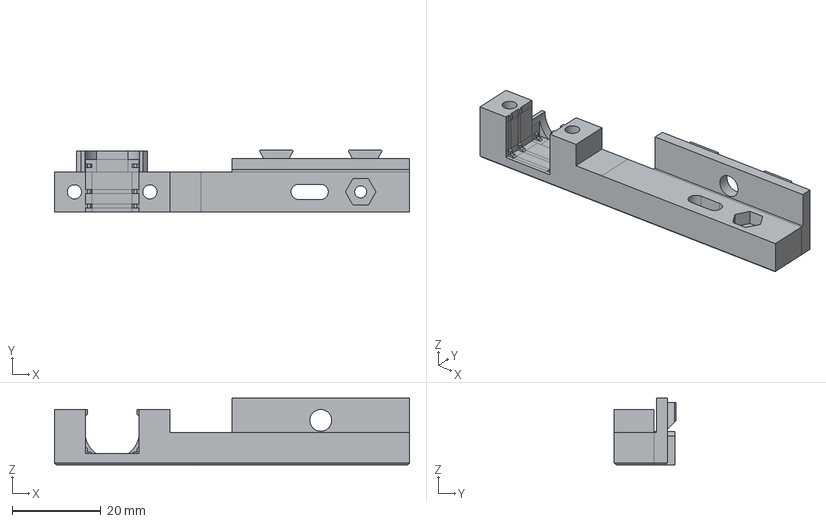
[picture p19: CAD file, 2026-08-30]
STEP+STL_(Parts)/STEP/GBP_Frame.step
80.0 x 13.9 x 15.0 mm

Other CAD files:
STEP+STL_(Parts)/STEP/03_Multicolor_arm/GBP_Arm_multicolor_nyloc.step
STEP+STL_(Parts)/STL/01_Mounts/AT_Style-Voron_Trident/ATmount_front_arm_base_(GBP).stl
STEP+STL_(Parts)/STEP/01_Mounts/ArmoredTurtle_Brush_mount/mount_upper.step
STEP+STL_(Parts)/STEP/01_Mounts/AT_Style-Voron_Trident+2.4/ATmount_front_arm_slide_(GBP).step
STEP+STL_(Parts)/STEP/01_Mounts/AT_Style-Voron_Trident+2.4/ATmount_front_arm_base_(GBP).step
STEP+STL_(Parts)/STEP/01_Mounts/AT_Style-Voron_Trident+2.4/ATmount_lower_(GBP).step
STEP+STL_(Parts)/STEP/01_Mounts/ArmoredTurtle_Brush_mount/[a]_front_arm_slide.step
STEP+STL_(Parts)/STEP/01_Mounts/Universal_Klicky_style/Klickystyle-basic.step
STEP+STL_(Parts)/STEP/01_Mounts/Universal_Klicky_style/Klickystyle-long.step
STEP+STL_(Parts)/STEP/01_Mounts/Universal_Klicky_style/Klickystyle-offseted-xtralong.step
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

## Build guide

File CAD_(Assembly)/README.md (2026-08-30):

What the hell is FCStd? Thats FreeCAD. Designed in version 1.0  
Why do I use FreeCAD? Because I am a masochist, thats why.  

CAD files for BRANTA are not available yet

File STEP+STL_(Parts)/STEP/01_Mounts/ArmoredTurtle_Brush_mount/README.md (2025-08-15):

Unmodified STEP files for AT Brush mount. Full attribution to AT team. For more information visit Armored Turtle website and/or Github  
Published under GPL-3 licence

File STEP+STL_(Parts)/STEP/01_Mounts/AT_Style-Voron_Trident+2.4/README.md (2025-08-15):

Modified version of AT Brush mount, suitable for Voron Trident.  
  
Based on: AT_Brush (Published under GPL-3) - Credit goes to ArmoredTurtle team

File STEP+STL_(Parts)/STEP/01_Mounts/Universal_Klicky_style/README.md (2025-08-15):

Universal mounting solution based on Klicky probe adjustable dock mount.  
  
Based on: Klicky-Probe (Published under GPL-3) - Credit goes to jlas1

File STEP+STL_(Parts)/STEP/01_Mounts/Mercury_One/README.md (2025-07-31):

Fixed mount for Mercury One, intended to be mounted to the front of printer. Experimental part, needs to be verified.

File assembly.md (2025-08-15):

# Goose Belt Purger assembly

## Preparation steps
a) Identify, if your board has protective flyback diodes. You can check the comprehensive list [here](board_list.md),. If not or you are in doubt, you will have to add it yourself to motor terminals. At this moment there are no known boards with RC snubber integrated, so expect to add snubber either way.
  
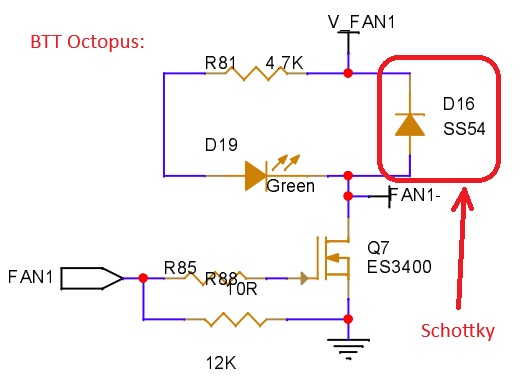
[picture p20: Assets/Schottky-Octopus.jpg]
  
_Example of BTT Octopus with Schottky diode on board_  
  
b) Install heatset inserts into **GBP_Idler** (1x) and **GBP_Deflector** (2x). If you want to use HSI variant arm, install insert also to **GBP_Arm_HSI** (1x). If you plan to use an AT style or Klicky style mount, you can also install inserts in those parts.  
c) Remove integrated support of **GBP_Deflector_(long/short)**. Grab the small bridging element in the middle with small pliers and remove it with twisting motion. It should easily and cleanly detach.   

## Assembly steps
1. _(Skip this step if you are using MicroFlip board. Instead just solder MicroFlip to your motor)_  
   Solder wires to the motor. If your board does not have sufficient protection, solder a schottky flyback diode and/or RC snubber to the motor terminals together with wires  
  **_1a._** Correct polarity of the motor is needed. Output shaft of the motor should be turning CCW (or CW if you printed mirrored version). If you can, test the polarity beforehand. In case the motor spins other way, switch the wires. If you are not adding flyback diode, you can reverse them later on in connector. If you are adding flyback, you will need to revert them directly on the motor.  
  **_1b._** Schottky flyback diode has a set polarity and you need to solder its cathode to the motor terminal where positive voltage (+) wire is connected. Cathode is usually marked with a colour stripe. Other end of diode shall go directly to the other motor terminal. Double check the polarity, because doing this wrong may overload and damage your control board.  
  **_1c._** RC snubber is formed of a capacitor and a resistor. One leg of each component shall be soldered together (in series) and other legs to the motor terminals (one resistor leg to one motor terminal, one capacitor leg to other motor terminal). RC snubber does not have set polarity and it does not matter which way around do you solder it.  
   
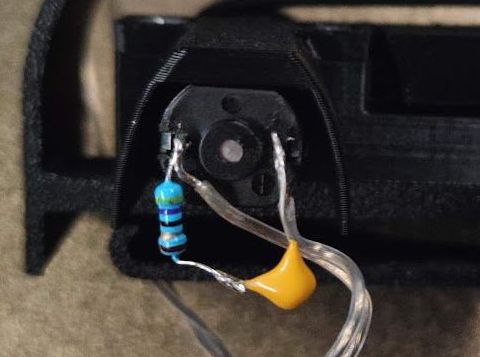
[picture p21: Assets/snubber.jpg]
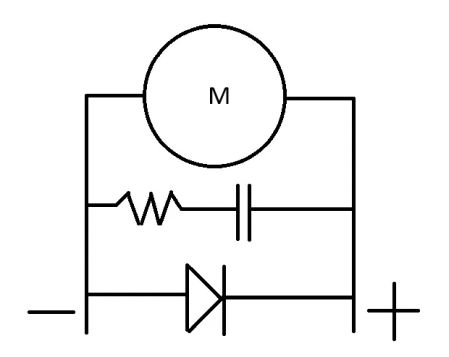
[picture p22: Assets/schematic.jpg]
    
_Example of snubber; schematic of snubber with diode_
   
2. Insert the motor to a slot in **GBP_Frame**. It should fit tightly, but not deform the part. Depending on your gearbox configuration you may have some play in axial direction. Try to place your motor in such a way, that the face with output shaft  is as flush with frame as possible.  
3. Clamp the motor from top with **GBP_Motor_cover**, push through 2x M3x20 FHCS screws, add **GBP_Deflector** to bottom and screw it together.  
4. Insert two of the bearings and one magnet into **GBP_Arm**. Bearings should be inserted from flat side (one with logo on it). Polarity of the magnet does not matter. If it is too loose, you may fix it with a drop of glue, but this should generally not be needed. Magnets act as a spring pulling arm away from mount and as such are being pushed into a pocket.  
5. Put M3x30 screw through remaining bearing, add **GBP_Bearing_spacer** on screw, then push the screw through arm opening and second bearing. Set the third bearing flush into hole and screw on **GBP_Idler**. Idler has to be fully tightened against bearing, but has to move freely. Do not overtighten, as it can damage your bearings.    
6. Put other magnet into Frame. Make sure to orient it in such a way, that it will repulse the magnet in Arm, when they are faced aginst each other.  
7. Slide the arm on the motor shaft, through remaining bearing. Make sure the arm can freely move up and down and that it gets pushed away from frame by magnets. Place nyloc nut to slot on top of arm _(does not apply to HSI variant)_ Secure the arm to mount with M3x20 SHCS _(M3x16 SHCS for HSI variant)_ screw (do not fully tighten). 
8. Push the M3 nut into a slot in **GBP_Motor_pulley** and screw in a set screw. You may need to push a nut deep inside with a screwdriver.  _Some users skip this step. This is ok, but can lead to pulley wobbling_
9. Push the pulley into the motor shaft. Push it as far as you can, but leave a tiny gap so that the arm is free to move. Tighten the set screw against motor shaft.  
10. Take the wristband, turn it inside out, slightly stretch it by hand and slide it on the pulley and idler. You don't need to put it into any specific position, it will self align when switched on.  
11. Test the assembly. Verify, that the motor turns when powered, that the arm can move and that the belt keeps turning without slipping off the pulleys. 

## Mount assembly and integration into printer
Purger is designed to be compatible with ArmoredTurtle brush mount and regarding its assembly, you should refer to AT's wonderful manual located [**here**](https://www.armoredturtle.xyz/manual.html?manual=at_brush&step=1)  
Keep in mind, if you have a Voron Trident or comparable printer, you will need to use modified parts provided in this repo, to shorten the horizontal reach of AT mount by 10 mm.  
  
Once you have your AT mount assembled, mount it to your printer to desired location and attach the Goose Belt Purger to it. If your printer is properly tuned, GBP should mate with AT mount firmly, without any residual movement, but also without need for excesive force to mate them. If they are too hard to assemble, you can gently sand the sides of dovetail wedges on frame. If they are too loose, you can shim the purger with a piece of paper or thin plastic placed in between purger's frame and AT mount.  
Once everything is in place, you can adjust it to right position using screws in AT mount. Horizontal adjustement screw gets exposed when you remove M3x16 SHCS screw and lift the arm up. Don't forget to put this screw back once you are done.  
You should adjust the Z position in such a way, that there is a tiny gap between nozzle and wristband. You can use the M3x20 SHCS screw for fine adjustement.  
In case you choose HSI arm variant, you should secure your screw with threadlocker or any other mean. If you don't, your screw will eventually fall out due to vibrations.
  
If you decide to use Klicky style mount or other kind of mount, assemble and tune it in simillar manner.  

## Troubleshooting and FAQ
- My wristband shifts partially/fully off the pulleys towards bed - this is most likely due to bad tolerance of a bearings holding the idler and/or missing M3x16 SHCS screw. Some cheaper bearings allow the idler or arm to be pulled to the side by a band tension, which causes this shifting off. If you can, use a better bearing. Otherwise try using **GBP_Idler(+3,0)**  
- My wristband shifts too far in, towards motor - less common, could be due to arm being warped. Try using **GBP_Idler(+0)**

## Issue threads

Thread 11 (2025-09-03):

Alternative Motor Driving w/ DRV8837?

piotrb, 2025-09-03:
Hi,

For an entirely different project I ended up picking up a couple of these DRV8837 boards .. its supposed to be a DC motor driver (https://www.aliexpress.com/item/1005007314034356.html)

Wondering if this would act sufficiently well to allow driving of the motor and also provide the protection needed.

Thanks

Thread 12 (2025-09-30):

Z

bavery79, 2025-09-30:
Thanks for the great work! Not sure if this is just a unique issue with my Happy Hare setup or might apply to other users trying to run this with a gantry mounted purger and no z-movement.  In my case, HH only automatically homes X & Y before loading the first filament at the beginning of a print.  This results in an error when attempting to call the _goose_purge_hh macro because z is not homed.  I would like to request that instead of setting the z_purge to the printer's z-position when z_purge == false, simply leave the z axis completely out of those two G1 movements, so as not to trigger an error in instances like this where the z axis hasn't been homed yet.

Graylag-PD, 2025-10-02:
Thank you for your report. I have not heard about anyone who would be loading their filament before fully homing all axes, as the homing (and bed leveling) is usually done before filament is loaded - which means this might be issue unique to you. Nevertheless, the macro still should be able to handle this kind of use case or at the very least graciously handle situation when Z is not homed (i.e. throw the error message explaining what is going on instead of falling back to klipper error).

As this issue seems unique to you I propose to not patch it in current branch of macro and instead fix it in upcoming refactored v1.0.0, which I am working on at this moment. You seem to understand the working of the macro, so I propose you make your own customized version without those Z movements. I am open to discussion though, if you would like different kind of immediate solution.

As for anyone else coming here with this kind of issue, if this is also your case, let me know and I will either post here temporary solution or patch current branch.

bavery79, 2025-10-04:
Thank you.  Yes, the edit to the macro is working just fine for me.  I think the pre-print issue stems from happy hare's "variable_load_initial_tool" option that when enabled loads the filament before the print actually starts.  In this case HH has some provision for homing if necessary, but is only homing the required axes so no Z homing in my case (might be a way to change that though... I'll have to look at that since that would eliminate the issue completely as well).

Additionally, the other time this comes into play is when attempting to manually change or load filaments when no print is running.  In this case, I believe there might also be something in happy hare to apply different logic to non-printing filament swaps and leave out the purge after loading, but I do prefer being able to purge automatically at these times as well...

Anyway, thanks for considering this.

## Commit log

2025-06-03 Initial data upload
    CAD data based on a005 iteration
    [belt_purger-Arm.step, belt_purger-Deflector.step, belt_purger-Deflector_noinserts.step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]
2025-06-04 Update goose_belt.cfg
    Fixed an issue with the script
    [goose_belt.cfg]
2025-06-14 Updated macro to accept LENGTH as parameter
    [goose_belt.cfg]
2025-06-20 Update goose_belt.cfg
    Added code for fan control, partial fix for premature delayed_gcode activation, and general cleanup of the code
    [goose_belt.cfg]
2025-06-23 Update README.md
    Added notes on desired speed of belt and motor selection
2025-07-06 Update goose_belt.cfg
    Reworked configuration file. Configuration variables are rearranged to be easier to understand. Additional features added:
    - Automated purge segment calculation based on min/max values
    - Speed up of belt during dwell phase
    - Speed up of belt during final belt cleaning phase
    [goose_belt.cfg]
2025-07-08 7th CAD iteration
    [belt_purger_a007.FCStd, belt_purger_a007.step]
2025-07-12 a008 CAD model
    [belt_purger_a008.FCStd, belt_purger_a008.step]
2025-07-20 a009 CAD upload
    [belt_purger_a009.FCStd]
2025-07-20 a009 CAD fix 1
    Replaced M3x20 SHCS for M3x16 SHCS
    [belt_purger_a009.FCStd]
2025-07-20 a009 fix2
    corrected visibility of deflector parts
    [belt_purger_a009.FCStd]
2025-07-20 Upload of new STEP files
    [ATmount_front_arm_base_(GBP).step, ATmount_front_arm_slide_(GBP).step, GBP_Arm.step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]
2025-07-20 Configuration v0.6.0
    Added support for Z axis movement
    [goose_belt.cfg]
2025-07-31 Preparation for Beta release
    [ATmount_front_arm_base_(GBP).step, ATmount_front_arm_slide_(GBP).step, ATmount_lower_(GBP).step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]
2025-08-01 goose_belt.cfg v0.6.1
    - fixed division by zero issue
    - fixed missing "printer.toolhead" statements
    - added default_purge_volume variable and associated logic
    [goose_belt.cfg]
2025-08-01 Pre release docs update
    [goose_belt.cfg]
2025-08-01 config v0.6.2
    User end script added
    [goose_belt.cfg]
2025-08-03 Update README.md
    Modified disclaimer
    added link to Printables
2025-08-05 v0.7.alpha1
    Changed input parameters from LENGTH and VOLUME to PURGE_LENGTH and PURGE_VOLUME, old parameters remain, but cause deprecation message.
    Added M118 reporting before and after purge
    Added sanity check for filament diameter (prevents division by zero or otherwise weird results)
    Minor adjustements
    It is no longer possible to override default purge volume by requesting VOLUME=0. Instead it is needed to input PURGE_VOLUME=-1
    [goose_belt.cfg]
2025-08-05 0.7.alpha2
    fix of '+' error
    [goose_belt.cfg]
2025-08-05 0.7.alpha3
    fixed '||' and '&&' errors
    [goose_belt.cfg]
2025-08-05 v0.7.0
    - Added new PURGE_ parameters and deprecated old ones
    - Added reporting before and after purge
    - Improved sanity checks
    - minor tweaks
    [goose_belt.cfg]
2025-08-08 experimental parts
    Motor cover for MicroFlip
    New deflector with uniform gap
    [GBP_Deflector_long_noinserts_uniformgap.step, GBP_Motor_cover_MicroFlip.step]
2025-08-11 multicolor arm
    [GBP_Arm_base.step, GBP_Arm_goose_cheek.step, GBP_Arm_goose_eye.step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]
2025-08-12 multicolor arm update 1
    Changed heatset to locknut
    [GBP_Arm_base.step]
2025-08-12 multicolor arm update 2
    [GBP_Arm_base_HSI.step, GBP_Arm_base_locknut.step]
2025-08-12 v0.7.1
    Added macro wrapper for Happy Hare
    [goose_belt.cfg]
2025-08-15 CAD a011 upload
    [ATmount_Voron_Trident.stl, ATmount_front_arm_base_(GBP).step, ATmount_front_arm_base_(GBP).stl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]
2025-08-15 corrections to a011 upload
    [ATmount_front_arm_base_(GBP).step, ATmount_front_arm_base_(GBP).stl, ATmount_front_arm_slide_(GBP).step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]
2025-08-22 v0.7.2alpha1
    - Fixed behaviour, that purging ends in deretraction instead of retraction
    - Added new variables `final_retraction` and `final_retraction_fr`, which allows for different retraction setting at the end of the macro
    - Changed handling of negative value `PURGE_LENGTH` to match behaviour of `PURGE_VOLUME`. Either of those parameters, when set to negative value, cause a dry purging run, overriding default purging volume
    [goose_belt.cfg]
2025-08-22 v0.7.2
    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
    [goose_belt.cfg]
2025-08-30 am02 mount variant
    [ATmount_front_arm_slide_offseted_am01.step, ATmount_front_arm_slide_offseted_am02.step]
2025-09-01 offset mount am04
    [ATmount_front_arm_base_(GBP).step, ATmount_front_arm_slide_(GBP).step, ATmount_front_arm_slide_offseted_am01.step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]
2026-05-13 Cover for MF2
    [GBP_Motor_cover-MicroFlip2.step, GBP_Motor_cover-MicroFlip2.stl]
